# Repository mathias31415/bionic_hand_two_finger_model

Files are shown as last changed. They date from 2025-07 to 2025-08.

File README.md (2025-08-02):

# bionic_hand_two_finger_model

This repository contains the outcomes of the project focused on developing a two-finger model of a bionic hand. The work was conducted by **Mathias Fuhrer, Tobias Klausmann, Jens Polzien, and Thomas Rapp** at **Hochschule Karlsruhe (H-KA**) during the summer semester of 2022.

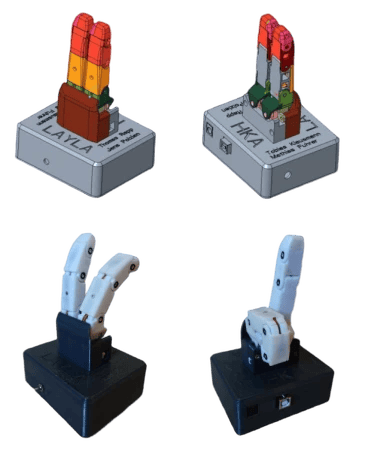
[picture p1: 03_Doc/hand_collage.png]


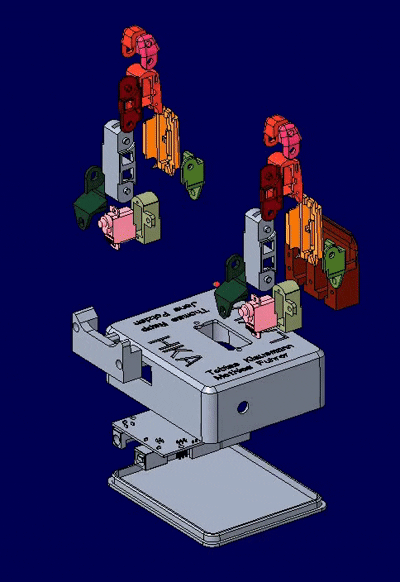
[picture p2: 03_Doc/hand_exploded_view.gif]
gif


## Demo video
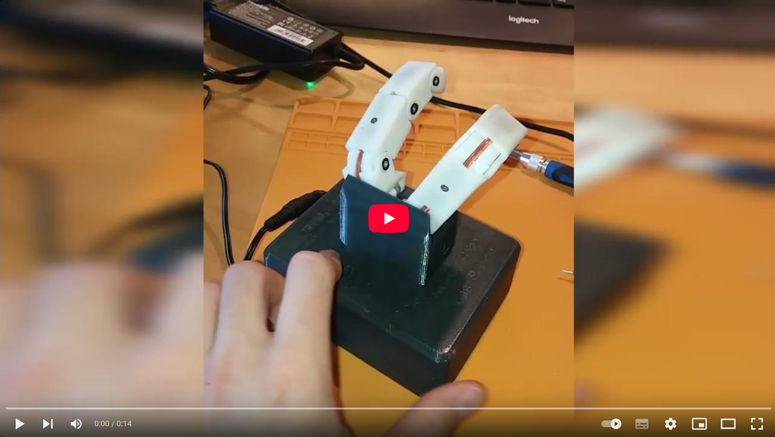
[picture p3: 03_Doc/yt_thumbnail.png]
video (https://youtu.be/Y5HJTN2VO6Q)


## Bill of Materials – Purchased Components
| Description | Quantity | Manufacturer |
|---|---|---|
| Micro Servo BMS-101HV | 6 | Bluebird |
| Servo HS-40 | 2 | Hitec |
| Arduino Uno | 1 | Arduino |
| Toggle switch | 1 | — |
| Countersunk screw M2 | — | — |
| Cylinder head screw M3 | — | — |
| Perforated circuit board 70x30mm| 1 | — |
| Barrel socket | 1 | — |

## Bill of Materials – Additive Manufactured Parts
| Description | Quantity | Manufacturing Method |
|---|---|---|
| Joint1_top (Gelenk1_oben) | 2 | SLA |
| Joint1_bottom (Gelenk1_unten) | 2 | SLA |
| Link1_top (Glied1_oben) | 2 | SLA |
| Link1_bottom (Glied1_unten) | 2 | SLA |
| Link2_right (Glied2_rechts) | 2 | SLA |
| Link2_left (Glied2_links) | 2 | SLA |
| Link3_right (Glied3_rechts) | 2 | SLA |
| Link3_left (Glied3_links) | 2 | SLA |
| Spreader_servo_holder (Spreizen_servohalter) | 2 | SLA |
| Palm_finger_holder (Mittelhand_Fingerhalter) | 1 | FDM |
| Palm_bottom (Mittelhand_unten) | 1 | FDM |
| PCB_mount (Halter_Leiterplatte) | 1 | FDM |
| Lid (Deckel) | 1 | FDM |

## Servo Preparation for Finger Integration
| Work Step | Tools | Illustration |
|---|---|---|
| Three micro servos (Blue Bird - BMS 101DMG) for bending and one Hitec HS-40 for spreading must be modified. | – | |
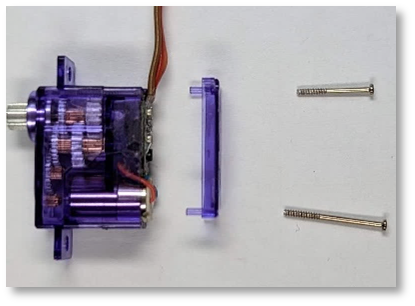
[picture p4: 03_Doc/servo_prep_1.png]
| Open the servo housing by removing the two screws. Keep them for reassembly. Remove the bottom cover. | Screwdriver |   |
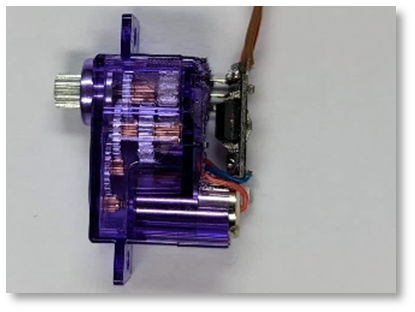
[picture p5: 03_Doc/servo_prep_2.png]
| Remove ~5mm of the housing around the PCB to make space for the joint bearing. Cut off the mounting flanges. | Cutter knife, side cutter |   |
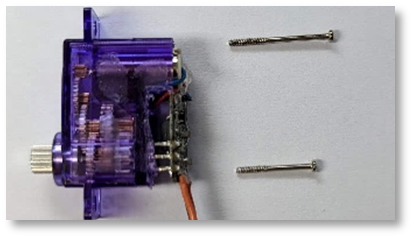
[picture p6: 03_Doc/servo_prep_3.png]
| Reinsert the screws until they are flush with the housing surface. | Screwdriver |   |
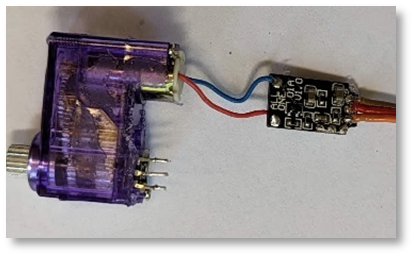
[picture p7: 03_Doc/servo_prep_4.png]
| Desolder the angle sensor (potentiometer) from the PCB. Carefully remove the PCB, which is now only attached to the motor wires. | Soldering iron, desoldering pump, desoldering braid, solder |  |
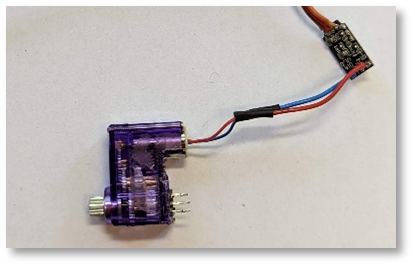
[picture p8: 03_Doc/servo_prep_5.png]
| Extend motor wires of one servo by ~3 cm. | Soldering iron, solder, wire extensions, heat shrink, heat gun, side cutter, wire stripper |   |
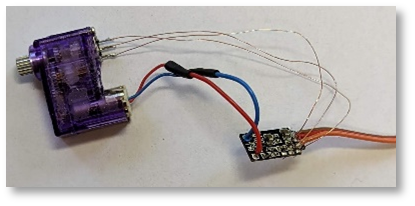
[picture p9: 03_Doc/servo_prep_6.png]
| Resolder the three angle sensor pins to the PCB using ~6cm long enameled copper wires. | Soldering iron, solder, side cutter, enameled copper wire |   |
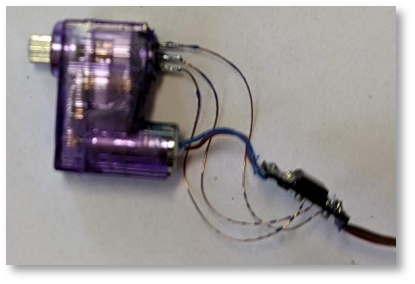
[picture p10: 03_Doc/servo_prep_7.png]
| For the other two servos, resolder angle sensor with 4–5cm enameled copper wires; no motor wire extension needed. | Soldering iron, solder, side cutter, enameled copper wire, tweezers |   |
| Bend the angle sensor pins flat against the housing surface. | Tweezers | |
| Apply solder mask to protect solder joints from corrosion and shorts. | Solder mask |  |
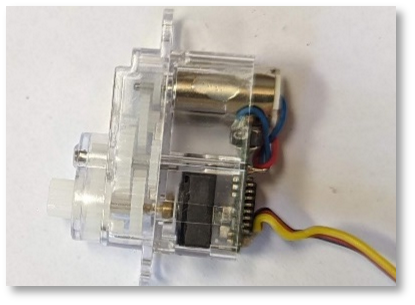
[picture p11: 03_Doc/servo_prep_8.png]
| For the Hitec HS-40, remove the glued bottom cover of the housing. | Flat-nose pliers, cutter knife, etc. |  |

## Assembly steps for building the finger

| Step | Tools | Illustration |
|---|---|---|
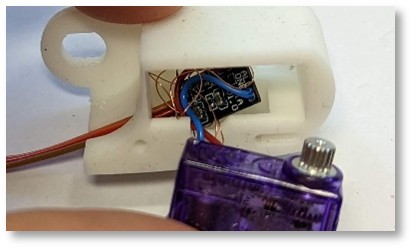
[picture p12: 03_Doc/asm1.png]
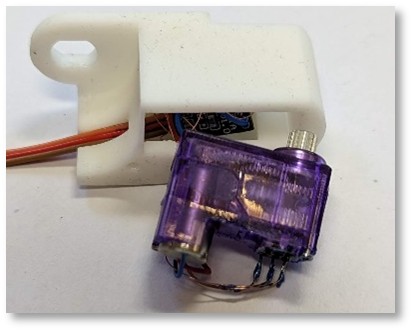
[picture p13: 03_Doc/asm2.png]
| First, the Blue Bird servo with extended motor and angle sensor cables must be installed into the middle finger segment. The circuit board is placed into the designated recess. The supply cable is routed through the slit to the outside. The two motor cables and three angle sensor cables must be placed in the intended cable guide. | Tweezers |    |
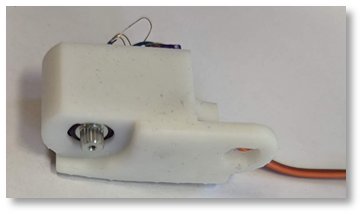
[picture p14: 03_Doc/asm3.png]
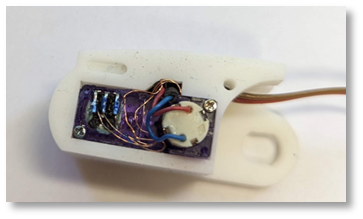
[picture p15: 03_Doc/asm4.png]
| The motor can now be slowly pushed into the finger segment as shown on the right. From the backside, through the hub opening, the circuit board and cables can be positioned with a tweezer. This is important so the servo can be fully inserted into the housing. Also ensure all excess cable lengths fit into the cavity of the circuit board. | Tweezers |    |
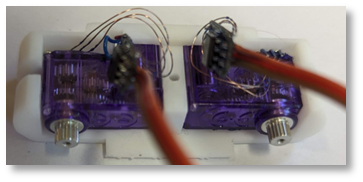
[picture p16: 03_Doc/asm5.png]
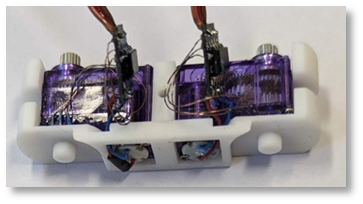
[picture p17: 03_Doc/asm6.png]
| The two remaining BMS 101 servos are installed in the base segment and positioned as shown in the picture on the right. The circuit board is placed on top of the servo and will be enclosed by the upper housing half. | Tweezers |   |
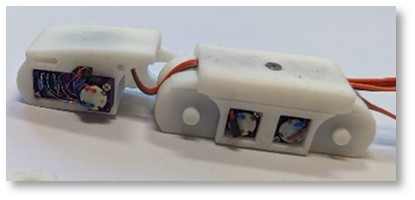
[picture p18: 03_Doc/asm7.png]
| The housing top can now be attached. The servo cable in the middle segment must be routed through the base segment. Cables are arranged in the provided cable ducts. To allow bending of the middle finger joint, a loop must be placed in the designated gap as shown on the right. The housing top is then screwed down with an M2 countersunk screw. Ensure all motor ends are aligned on the same side when positioning the finger joints. | Screwdriver, Tweezers |  |
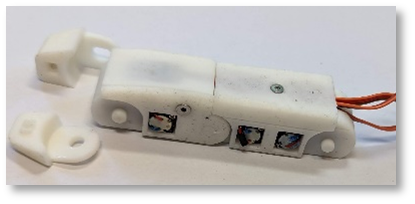
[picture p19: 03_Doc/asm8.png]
| The base and middle segments can be connected by attaching the second housing half of the middle segment. The halves are screwed together with an M2 countersunk screw. | Screwdriver, Tweezers |  |
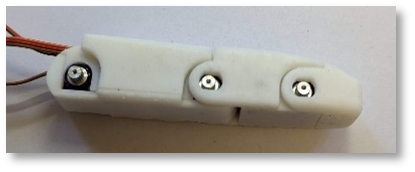
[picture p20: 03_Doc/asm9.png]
| The housing halves of the end segment seen in the previous step can now also be installed and secured with an M2 countersunk screw. | Screwdriver |  |
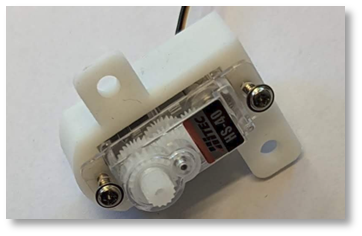
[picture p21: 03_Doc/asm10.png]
| The Hitec HS-40 servo is inserted into the spreading mechanism and fastened with the supplied screws to the SLA part. | Screwdriver |  |
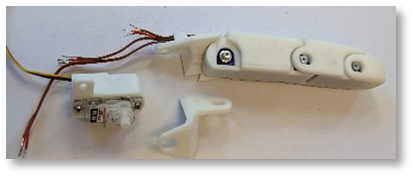
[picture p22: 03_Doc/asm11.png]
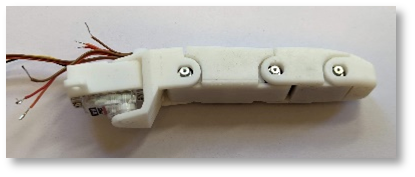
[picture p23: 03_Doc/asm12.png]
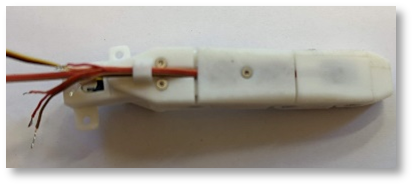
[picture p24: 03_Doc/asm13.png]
| This is the drive unit for the spreading function, which can now be connected to the rest of the finger. The last two SLA parts are assembled with two M2 countersunk screws. These two parts form the bearing for the bending function of the finger base joint as well as the spreading joint. The cables exiting the finger are routed through the designated cable channel. | Screwdriver |      |
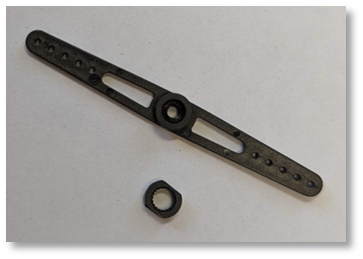
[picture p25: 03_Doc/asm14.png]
| The power transmission from the four servos to the SLA parts is realized by a modified adapter supplied with the servos. The adapter must be adjusted as shown in the image. Only the gearwheel is needed, and material is removed in parallel on two opposite sides. | Cutter, Side cutters, Sandpaper, File |  |
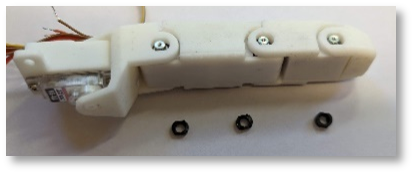
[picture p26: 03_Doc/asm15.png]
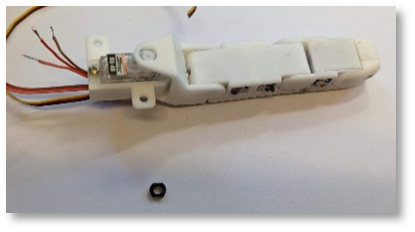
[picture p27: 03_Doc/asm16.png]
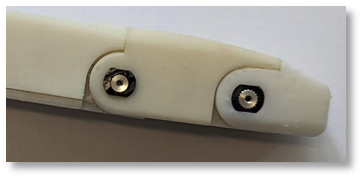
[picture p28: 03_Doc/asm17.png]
| The modified adapters are pressed onto the servo shafts, creating a form-fit power transmission between the servo and the finger segment. Before pressing in the adapter, ensure the servo is in the correct end position. This can be easily done using a servo tester or control via Arduino, for example. If there is any play, a new adapter must be made with slightly less material removed on the sides. If the adapter doesn’t fit into the recess, more material can be removed using a file or knife. | Cutter, Side cutters, Sandpaper, File |   |
| The above steps are then repeated for the second finger. The two fingers are then fastened to the Arduino and power supply housing. The power supply and Arduino board are also installed in the housing. Servo cables can be routed through the provided openings into the housing and connected with appropriate pins and power supply. Servo cables may need to be extended if necessary. | Soldering iron, Hot air gun, Tweezers, Screwdriver |  |
| The Arduino can then be programmed via the USB port placed on the outside. | USB cable, Programmer, Arduino software |  |

## Schematic
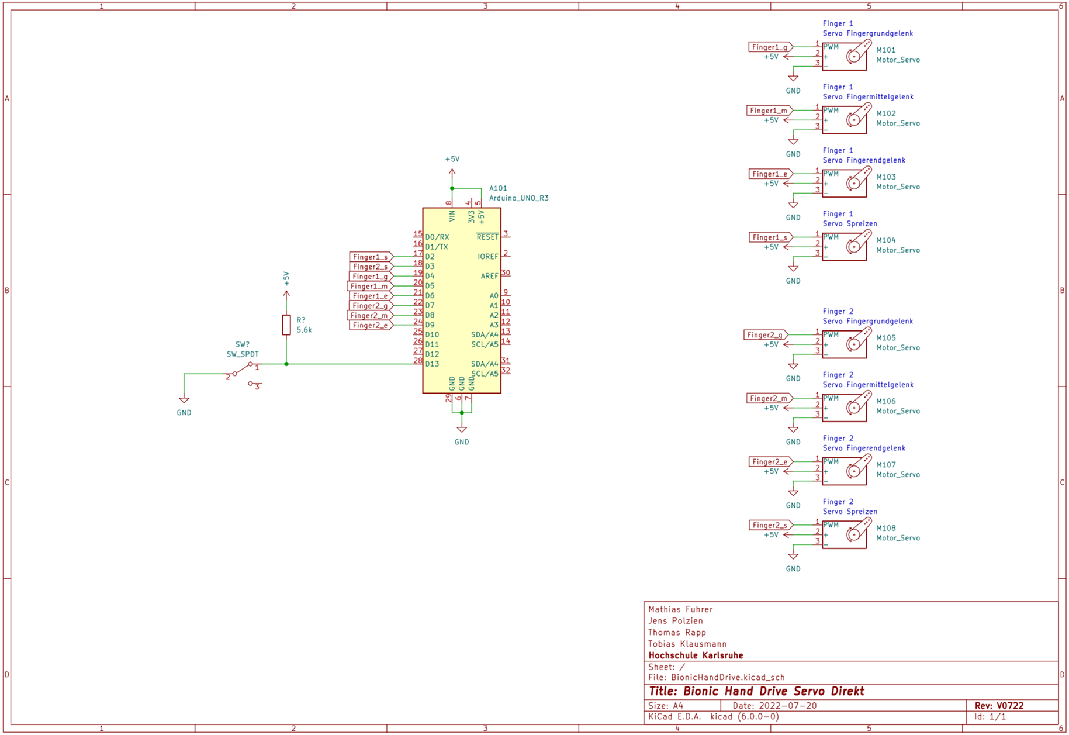
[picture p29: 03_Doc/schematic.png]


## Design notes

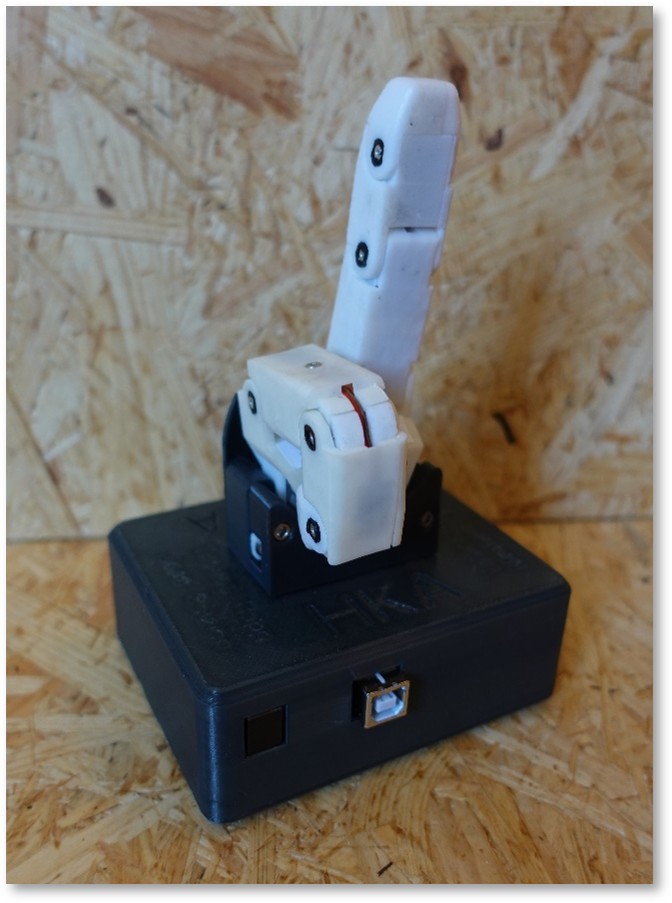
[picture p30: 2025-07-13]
03_Doc/asm_complete_2.png

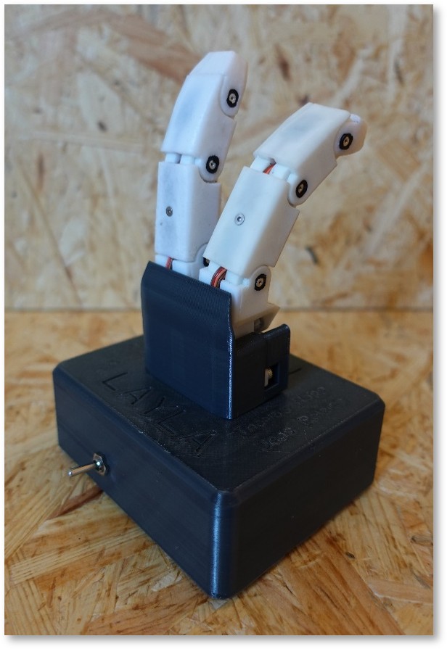
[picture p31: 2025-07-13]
03_Doc/asm_complete_1.png

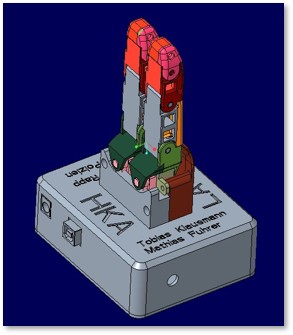
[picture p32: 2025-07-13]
03_Doc/cad_asm_complete_2.png

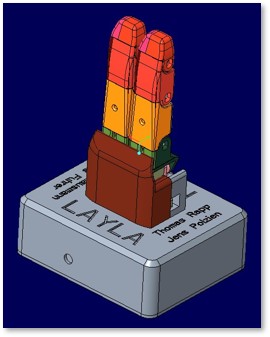
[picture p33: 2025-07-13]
03_Doc/cad_asm_complete_1.png

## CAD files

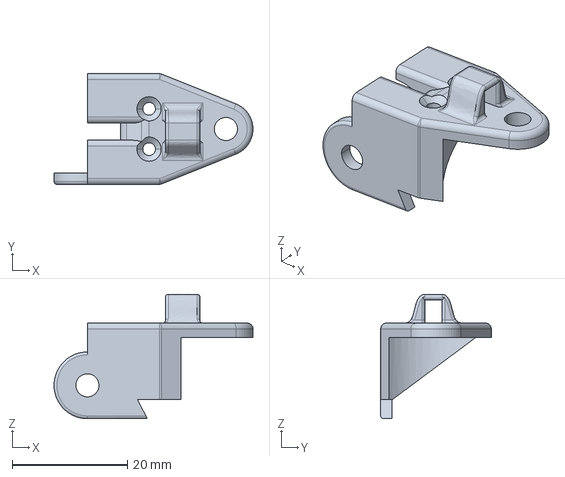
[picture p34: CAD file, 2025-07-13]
01_CAD/STP/gelenk1_oben_leitung.stp
34.5 x 19.2 x 21.6 mm

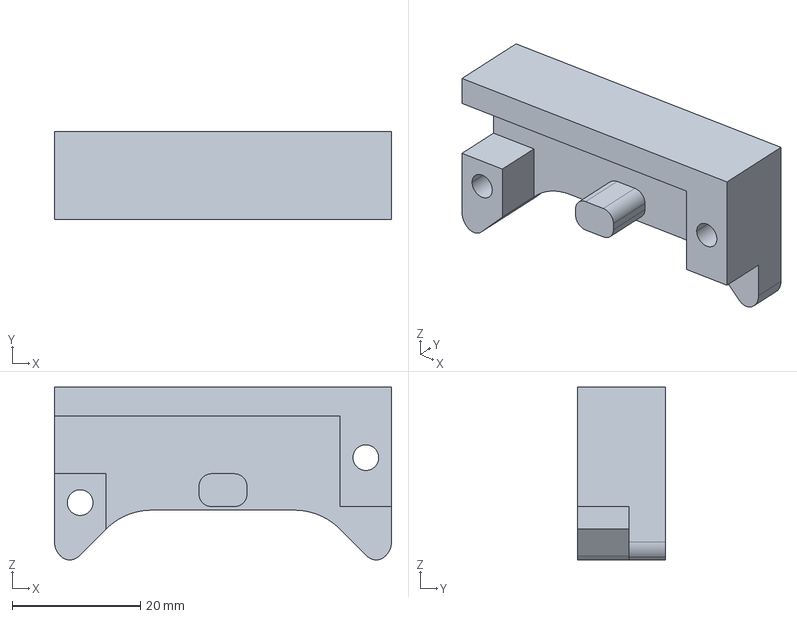
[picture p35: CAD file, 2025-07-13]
01_CAD/STP/mittelhand_unten.stp
52.5 x 13.7 x 26.9 mm

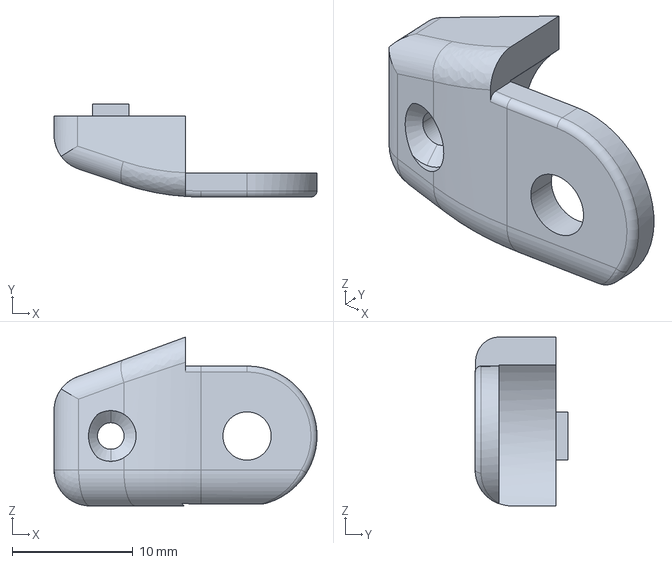
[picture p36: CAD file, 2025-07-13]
01_CAD/STP/glied3_links.stp
21.8 x 7.70 x 14.0 mm

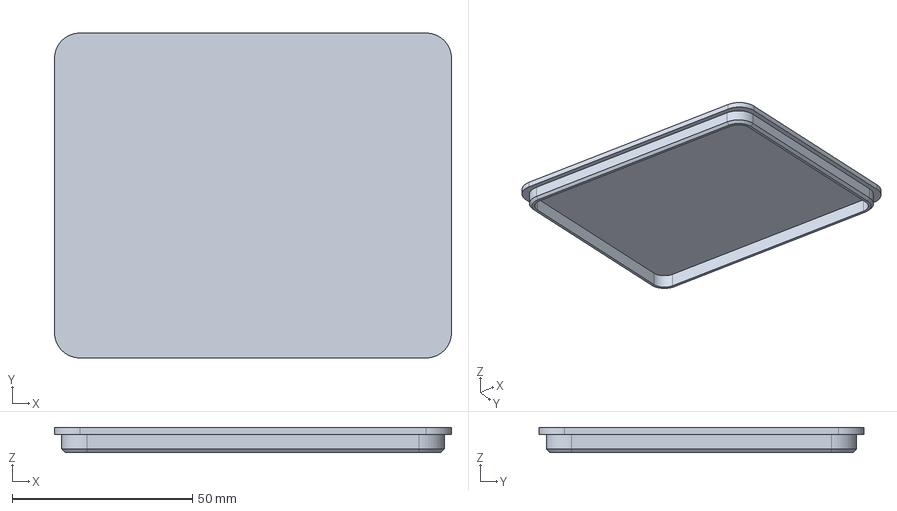
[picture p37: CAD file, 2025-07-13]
01_CAD/STP/deckel.stp
110.0 x 90.0 x 7.00 mm

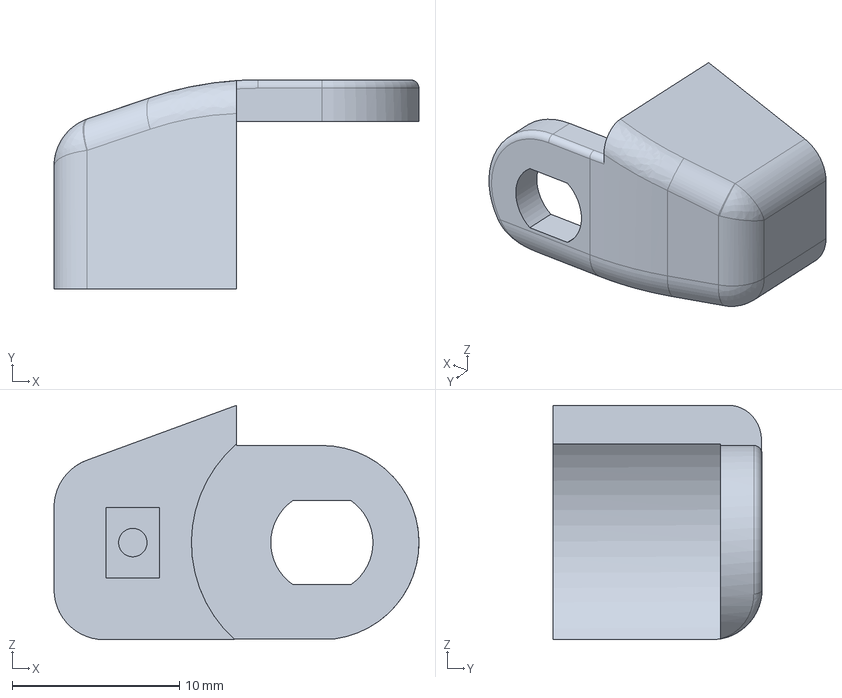
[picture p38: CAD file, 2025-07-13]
01_CAD/STP/glied3_rechts.stp
21.8 x 12.5 x 14.0 mm

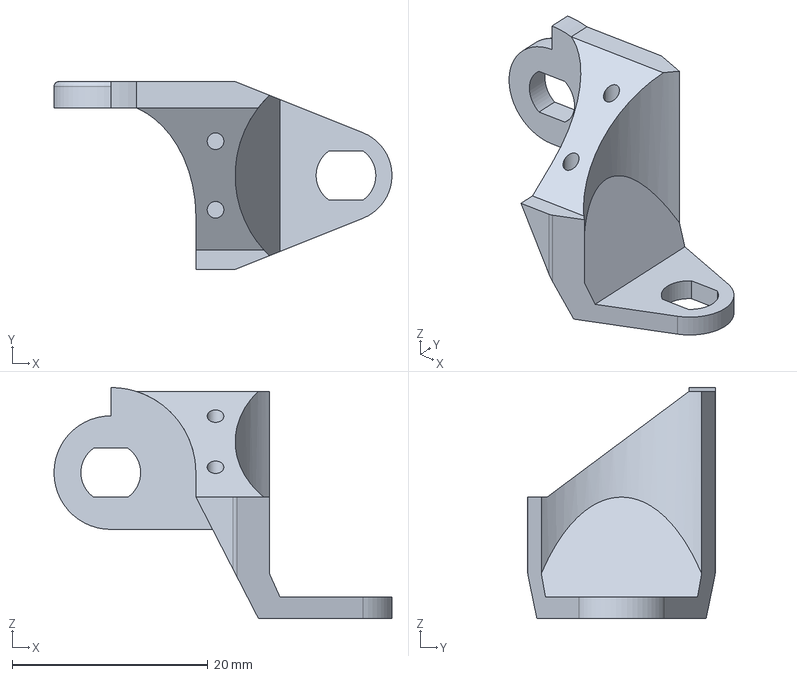
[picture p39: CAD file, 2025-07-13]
01_CAD/STP/gelenk1_unten.stp
34.5 x 19.2 x 23.6 mm

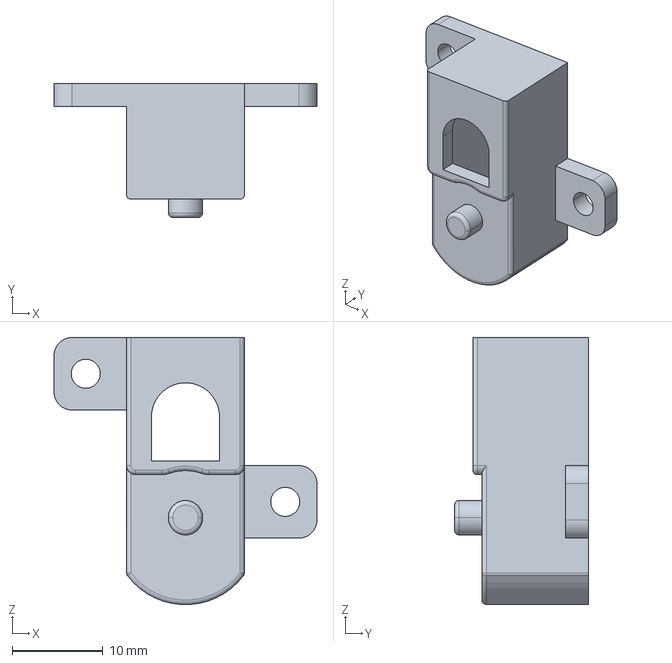
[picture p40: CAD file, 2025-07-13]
01_CAD/STP/motor_spreizen_halterung.stp
29.0 x 14.8 x 29.4 mm

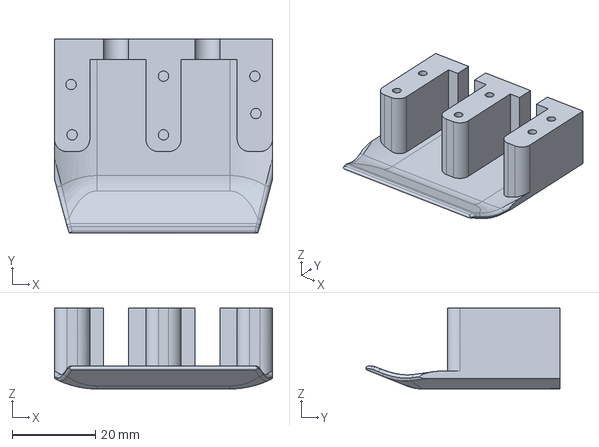
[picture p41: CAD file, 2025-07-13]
01_CAD/STP/mittelhand_fingerhalter.stp
52.5 x 46.8 x 19.5 mm

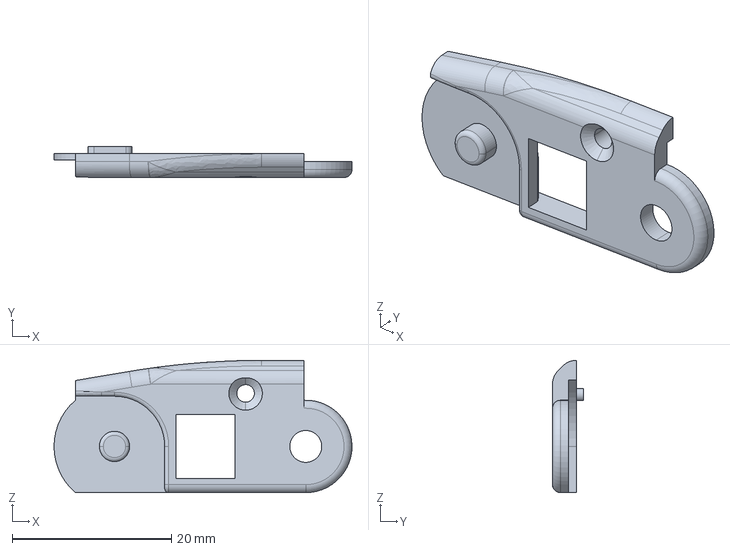
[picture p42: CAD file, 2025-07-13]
01_CAD/STP/glied2_links.stp
37.4 x 3.90 x 16.6 mm

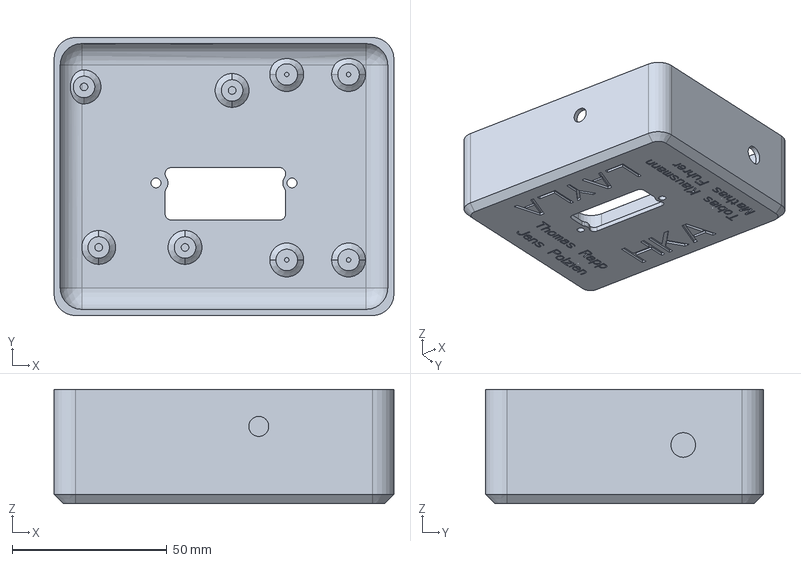
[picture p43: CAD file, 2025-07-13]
01_CAD/STP/halter_leiterplatte.stp
110.0 x 90.0 x 37.0 mm

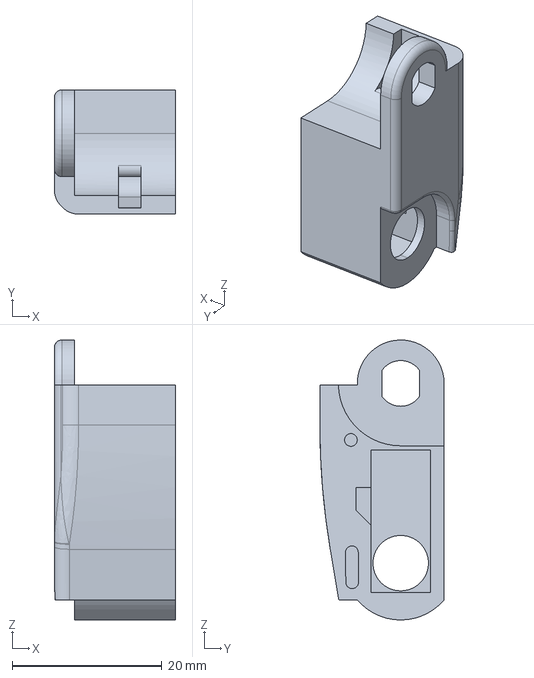
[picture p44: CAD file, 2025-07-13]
01_CAD/STP/glied2_rechts.stp
16.2 x 16.6 x 37.4 mm

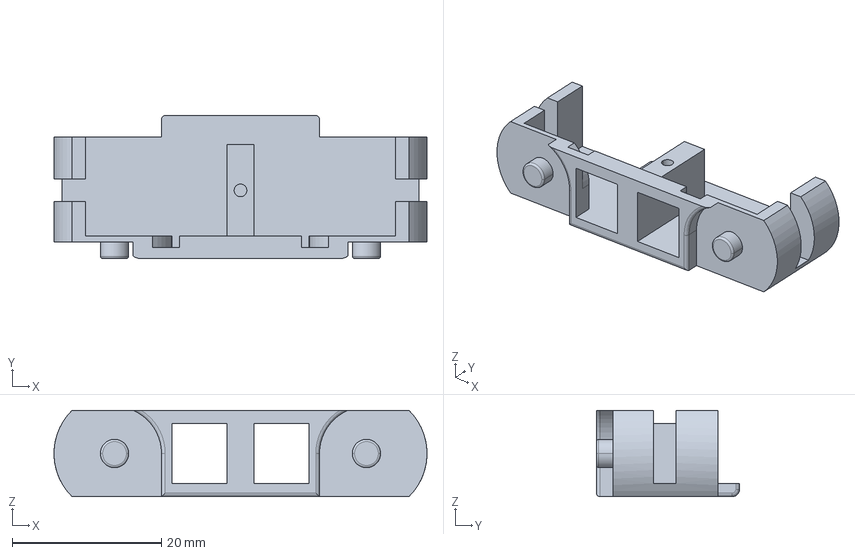
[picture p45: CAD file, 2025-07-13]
01_CAD/STP/glied1_unten.stp
50.1 x 19.2 x 11.6 mm

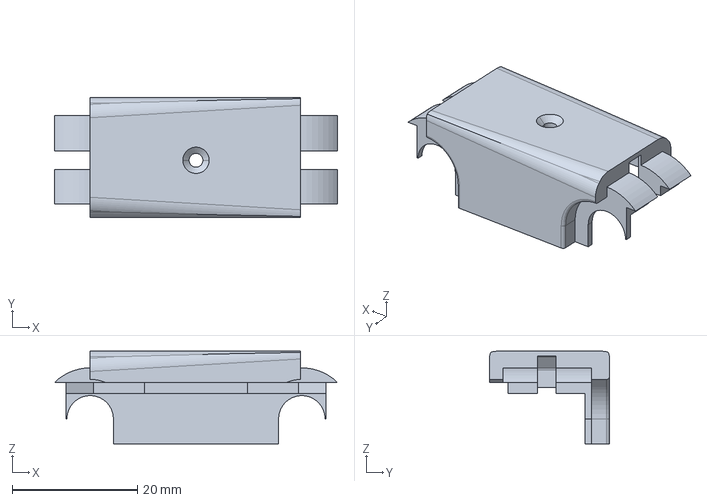
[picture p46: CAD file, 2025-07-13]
01_CAD/STP/glied1_oben.stp
45.2 x 19.2 x 14.8 mm

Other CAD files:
01_CAD/STL/deckel.stl
01_CAD/STL/gelenk1_oben_leitung.stl
01_CAD/STL/gelenk1_unten.stl
01_CAD/STL/glied1_oben.stl
01_CAD/STL/glied1_unten.stl
01_CAD/STL/glied2_links.stl
01_CAD/STL/glied2_rechts.stl
01_CAD/STL/glied3_links.stl
01_CAD/STL/glied3_rechts.stl
01_CAD/STL/halter_leiterplatte.stl
01_CAD/STL/mittelhand_fingerhalter.stl
01_CAD/STL/mittelhand_unten.stl
01_CAD/STL/motor_spreizen_halterung.stl

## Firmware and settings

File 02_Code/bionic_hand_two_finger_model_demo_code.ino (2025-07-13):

// Project:       Bionic Hand Drive
// Topic:         Motor control of servo motors
// Description:   This program controls six gestures of two fingers, each with four servo motors. The program runs on an Arduino Uno.

// Authors:       Mathias Fuhrer
//                Tobias Klausmann
//                Jens Polzien
//                Thomas Rapp

// Date:          21.07.2022

#include <Servo.h>                                    // Servo library

#define spread_Finger1_pin 2                          // Servo MG995                --> Spread middle finger
#define spread_Finger2_pin 3                          // Servo MG995                --> Spread index finger

#define Finger1_Joint_1_pin 4                         // Servo MG995                --> Bend middle finger
#define Finger1_Joint_2_pin 5                         // Servo MG995                --> Bend middle finger
#define Finger1_Joint_3_pin 6                         // Servo MG995                --> Bend middle finger

#define Finger2_Joint_1_pin 7                         // Servo MG995                --> Bend index finger
#define Finger2_Joint_2_pin 8                         // Servo MG995                --> Bend index finger
#define Finger2_Joint_3_pin 9                         // Servo MG995                --> Bend index finger

int buttonPin = 13;                                   // Set pin for button
int buttonPin_old;                                    // Variable to store previous button state
int gestureIndex = 0;                                 // Counter initialization
int numberOfGestures = 6;                             // Set number of gestures

Servo spread_Finger1;                                 // Initialize servo motor
Servo spread_Finger2;                                 // Initialize servo motor

Servo Finger1_Joint_1;                                // Initialize servo motor
Servo Finger1_Joint_2;                                // Initialize servo motor
Servo Finger1_Joint_3;                                // Initialize servo motor
Servo Finger2_Joint_1;                                // Initialize servo motor
Servo Finger2_Joint_2;                                // Initialize servo motor
Servo Finger2_Joint_3;                                // Initialize servo motor

// ------ Function declarations ------
void gestureRock();
void gesturePaper();
void gestureScissor();
void gestureMiddleFinger();
void gestureHalfPos1();
void gestureHalfPos2();
// -----------------------------------

void setup() {
  Serial.begin(9600);                                 // Initialize serial monitor with baud rate

  pinMode(buttonPin, INPUT);                          // Set button pin as input
  buttonPin_old = digitalRead(buttonPin);             // Store initial button state

  spread_Finger1.attach(spread_Finger1_pin);          // Attach servo to pin
  spread_Finger2.attach(spread_Finger2_pin);          // Attach servo to pin
  Finger1_Joint_1.attach(Finger1_Joint_1_pin);        // Attach servo to pin
  Finger1_Joint_2.attach(Finger1_Joint_2_pin);        // Attach servo to pin
  Finger1_Joint_3.attach(Finger1_Joint_3_pin);        // Attach servo to pin
  Finger2_Joint_1.attach(Finger2_Joint_1_pin);        // Attach servo to pin
  Finger2_Joint_2.attach(Finger2_Joint_2_pin);        // Attach servo to pin
  Finger2_Joint_3.attach(Finger2_Joint_3_pin);        // Attach servo to pin

  spread_Finger1.detach();                            // Detach servo to save energy
  spread_Finger2.detach();                            // Detach servo to save energy
  Finger1_Joint_1.detach();                           // Detach servo to save energy
  Finger2_Joint_1.detach();                           // Detach servo to save energy
  Finger1_Joint_2.detach();                           // Detach servo to save energy
  Finger2_Joint_2.detach();                           // Detach servo to save energy
  Finger1_Joint_3.detach();                           // Detach servo to save energy
  Finger2_Joint_3.detach();                           // Detach servo to save energy
}

void loop() 
{
  while(digitalRead(buttonPin) == buttonPin_old)      // Wait here as long as no button press is detected
  {
    delay (50);
  }
  
  buttonPin_old = digitalRead(buttonPin);             // Remember last button state
  Serial.println("Edge detected");                    // Continue program when button press detected
  gestureIndex = gestureIndex + 1;                    // Increase counter

  switch(gestureIndex)
  {
    case 1: gestureRock();                            // If counter gestureIndex = 1, call gestureRock
    break;
    case 2: gesturePaper();                           // If counter gestureIndex = 2, call gesturePaper
    break;
    case 3: gestureScissor();                         // If counter gestureIndex = 3, call gestureScissor
    break;
    case 4: gestureMiddleFinger();                    // If counter gestureIndex = 4, call gestureMiddleFinger
    break;
    case 5: gestureHalfPos1();                        // If counter gestureIndex = 5, call gestureHalfPos1
    break;
    case 6: gestureHalfPos2();                        // If counter gestureIndex = 6, call gestureHalfPos2
    break;
    default:
    break;
  }

  if(gestureIndex >= numberOfGestures)                // If last gesture reached ...
  {
    gestureIndex = 0;                                 // ... reset counter
  }
}

// ---------------------------------------- Gesture functions --------------------------------------------------------------------------

// ------ Info about servo end positions ------
// Bend Joint 1:
//   140°  - extended
//   35°   - bent
// Bend Joint 2 and 3:
//   35°   - extended
//   140°  - bent
// Spread:
//   90° center position +- approx. 10°
// ------ End of info ------------------------

void gestureScissor()
{
    spread_Finger1.attach(2);           // Attach servo
    spread_Finger2.attach(3);           // Attach servo
    Finger1_Joint_1.attach(4);          // Attach servo
    Finger2_Joint_1.attach(7);          // Attach servo
    Finger1_Joint_2.attach(5);          // Attach servo
    Finger2_Joint_2.attach(8);          // Attach servo
    Finger1_Joint_3.attach(6);          // Attach servo
    Finger2_Joint_3.attach(9);          // Attach servo
    
    spread_Finger1.write(90);           // no spreading
    spread_Finger2.write(90);           // no spreading
    Finger1_Joint_1.write(35);          // fully extended
    Finger2_Joint_1.write(35);          // fully extended
    Finger1_Joint_2.write(140);         // fully extended
    Finger2_Joint_2.write(140);         // fully extended
    Finger1_Joint_3.write(140);         // fully extended
    Finger2_Joint_3.write(140);         // fully extended
    delay(400);
    
    spread_Finger1.detach();            // Detach servo to save energy
    spread_Finger2.detach();            // Detach servo to save energy
    Finger1_Joint_1.detach();           // Detach servo to save energy
    Finger2_Joint_1.detach();           // Detach servo to save energy
    Finger1_Joint_2.detach();           // Detach servo to save energy
    Finger2_Joint_2.detach();           // Detach servo to save energy
    Finger1_Joint_3.detach();           // Detach servo to save energy
    Finger2_Joint_3.detach();           // Detach servo to save energy
}

void gestureRock()
{
    spread_Finger1.attach(2);           // Attach servo
    spread_Finger2.attach(3);           // Attach servo
    Finger1_Joint_1.attach(4);          // Attach servo
    Finger2_Joint_1.attach(7);          // Attach servo
    Finger1_Joint_2.attach(5);          // Attach servo
    Finger2_Joint_2.attach(8);          // Attach servo
    Finger1_Joint_3.attach(6);          // Attach servo
    Finger2_Joint_3.attach(9);          // Attach servo
    
    spread_Finger1.write(80);           // spread finger 1
    spread_Finger2.write(100);          // spread finger 2
    Finger1_Joint_1.write(139);         // fully bent
    Finger2_Joint_1.write(145);         // fully bent
    Finger1_Joint_2.write(35);          // fully bent
    Finger2_Joint_2.write(35);          // fully bent
    Finger1_Joint_3.write(35);          // fully bent
    Finger2_Joint_3.write(35);          // fully bent
    delay (400);
    
    spread_Finger1.detach();            // Detach servo to save energy
    spread_Finger2.detach();            // Detach servo to save energy
    Finger1_Joint_1.detach();           // Detach servo to save energy
    Finger2_Joint_1.detach();           // Detach servo to save energy
    Finger1_Joint_2.detach();           // Detach servo to save energy
    Finger2_Joint_2.detach();           // Detach servo to save energy
    Finger1_Joint_3.detach();           // Detach servo to save energy
    Finger2_Joint_3.detach();           // Detach servo to save energy
}

void gesturePaper()
{
    spread_Finger1.attach(2);           // Attach servo
    spread_Finger2.attach(3);           // Attach servo
    Finger1_Joint_1.attach(4);          // Attach servo
    Finger2_Joint_1.attach(7);          // Attach servo
    Finger1_Joint_2.attach(5);          // Attach servo
    Finger2_Joint_2.attach(8);          // Attach servo
    Finger1_Joint_3.attach(6);          // Attach servo
    Finger2_Joint_3.attach(9);          // Attach servo
    
    spread_Finger1.write(95);           // minimal spread to press fingers together
    spread_Finger2.write(85);           // minimal spread to press fingers together
    Finger1_Joint_1.write(139);         // fully extended
    Finger2_Joint_1.write(145);         // fully extended
    Finger1_Joint_2.write(35);          // fully extended
    Finger2_Joint_2.write(35);          // fully extended
    Finger1_Joint_3.write(35);          // fully extended
    Finger2_Joint_3.write(35);          // fully extended
    delay (400);
    
    spread_Finger1.detach();            // Detach servo to save energy
    spread_Finger2.detach();            // Detach servo to save energy
    Finger1_Joint_1.detach();           // Detach servo to save energy
    Finger2_Joint_1.detach();           // Detach servo to save energy
    Finger1_Joint_2.detach();           // Detach servo to save energy
    Finger2_Joint_2.detach();           // Detach servo to save energy
    Finger1_Joint_3.detach();           // Detach servo to save energy
    Finger2_Joint_3.detach();           // Detach servo to save energy
}

void gestureMiddleFinger()
{
    spread_Finger1.attach(2);           // Attach servo
    spread_Finger2.attach(3);           // Attach servo
    Finger1_Joint_1.attach(4);          // Attach servo
    Finger2_Joint_1.attach(7);          // Attach servo
    Finger1_Joint_2.attach(5);          // Attach servo
    Finger2_Joint_2.attach(8);          // Attach servo
    Finger1_Joint_3.attach(6);          // Attach servo
    Finger2_Joint_3.attach(9);          // Attach servo
    
    spread_Finger1.write(90);           // no spreading
    spread_Finger2.write(90);           // no spreading
    Finger1_Joint_1.write(140);         // fully bent
    Finger2_Joint_1.write(35);          // fully extended
    Finger1_Joint_2.write(35);          // fully bent
    Finger2_Joint_2.write(140);         // fully bent
    Finger1_Joint_3.write(35);          // fully bent
    Finger2_Joint_3.write(140);         // fully bent
    delay (400);
    
    spread_Finger1.detach();            // Detach servo to save energy
    spread_Finger2.detach();            // Detach servo to save energy
    Finger1_Joint_1.detach();           // Detach servo to save energy
    Finger2_Joint_1.detach();           // Detach servo to save energy
    Finger1_Joint_2.detach();           // Detach servo to save energy
    Finger2_Joint_2.detach();           // Detach servo to save energy
    Finger1_Joint_3.detach();           // Detach servo to save energy
    Finger2_Joint_3.detach();           // Detach servo to save energy 
}

void gestureHalfPos1()
{
    spread_Finger1.attach(2);           // Attach servo
    spread_Finger2.attach(3);           // Attach servo
    Finger1_Joint_1.attach(4);          // Attach servo
    Finger2_Joint_1.attach(7);          // Attach servo
    Finger1_Joint_2.attach(5);          // Attach servo
    Finger2_Joint_2.attach(8);          // Attach servo
    Finger1_Joint_3.attach(6);          // Attach servo
    Finger2_Joint_3.attach(9);          // Attach servo
    
    spread_Finger1.write(70);           // strongly spread
    spread_Finger2.write(75);           // strongly spread
    Finger1_Joint_1.write(50);          // slightly bent
    Finger2_Joint_1.write(120);         // strongly bent
    Finger1_Joint_2.write(100);         // slightly bent 
    Finger2_Joint_2.write(70);          // more bent
    Finger1_Joint_3.write(100);         // slightly bent
    Finger2_Joint_3.write(50);          // strongly bent
    delay (400);
    
    spread_Finger1.detach();            // Detach servo to save energy
    spread_Finger2.detach();            // Detach servo to save energy
    Finger1_Joint_1.detach();           // Detach servo to save energy
    Finger2_Joint_1.detach();           // Detach servo to save energy
    Finger1_Joint_2.detach();           // Detach servo to save energy
    Finger2_Joint_2.detach();           // Detach servo to save energy
    Finger1_Joint_3.detach();           // Detach servo to save energy
    Finger2_Joint_3.detach();           // Detach servo to save energy 
}

void gestureHalfPos2()
{
    spread_Finger1.attach(2);           // Attach servo
    spread_Finger2.attach(3);           // Attach servo
    Finger1_Joint_1.attach(4);          // Attach servo
    Finger2_Joint_1.attach(7);          // Attach servo
    Finger1_Joint_2.attach(5);          // Attach servo
    Finger2_Joint_2.attach(8);          // Attach servo
    Finger1_Joint_3.attach(6);          // Attach servo
    Finger2_Joint_3.attach(9);          // Attach servo
    
    spread_Finger1.write(70);           // strongly spread
    spread_Finger2.write(110);          // strongly spread
    Finger1_Joint_1.write(140);         // fully bent
    Finger2_Joint_1.write(70);          // more extended
    Finger1_Joint_2.write(140);         // fully extended
    Finger2_Joint_2.write(70);          // more bent
    Finger1_Joint_3.write(70);          // more bent
    Finger2_Joint_3.write(90);          // medium bent
    delay (400);
    
    spread_Finger1.detach();            // Detach servo to save energy
    spread_Finger2.detach();            // Detach servo to save energy
    Finger1_Joint_1.detach();           // Detach servo to save energy
    Finger2_Joint_1.detach();           // Detach servo to save energy
    Finger1_Joint_2.detach();           // Detach servo to save energy
    Finger2_Joint_2.detach();           // Detach servo to save energy
    Finger1_Joint_3.detach();           // Detach servo to save energy
    Finger2_Joint_3.detach();           // Detach servo to save energy 
}
